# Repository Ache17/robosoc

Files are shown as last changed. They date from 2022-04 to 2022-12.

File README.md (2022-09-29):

# Quala

### Description
The goal of the project is to create an open drone that could be used potentially in future for running future project. Some initial idea was to create a drone swarm ( smaller drones "scouters" and larger drones "tankers", [Alex's pitch text needed for that]). Overall we want to have: 
- an OK performance mechanics ( we got the good donations and have stuff from DJI ), 
- own flight controller ( or at least ported by us to ardupilot in order to understand it better and modify our system in future)
- Video processing, communication and streaming done on raspberry pi ( open source, easy to modify, used in university courses)
- Control ( or sending command) done by Laptop

### System Diagram :
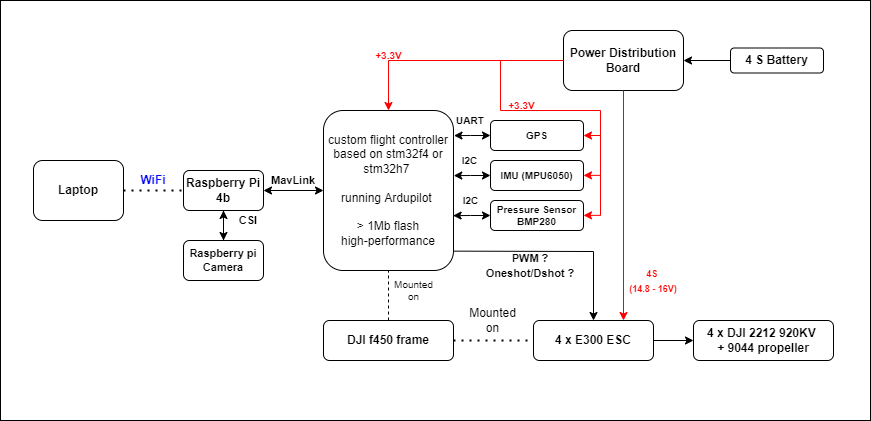
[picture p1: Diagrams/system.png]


## Components :
- Frame : [DJI F450](https://www.unmannedtechshop.co.uk/product/f450-quadcopter-frame-with-integrated-pdb/) 
- Autopilot : [Ardupilot](https://ardupilot.org/)
- ESCs : [E300](https://www.dji.com/uk/e300) (used now) or [XXD 30A](https://uk.banggood.com/Wholesale-XXD-HW30A-30A-Brushless-Motor-ESC-For-Airplane-Quadcopter-p-50621.html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) ( just because of cheap, maybe utilized in future)
- Motors : DJI 2212 motor 920kv ( standard DJI motors that came with the motors)
- Controller : Designed by us Board with stm32f411 or stm32h745/755 
- Video Processing / Communication (WiFi) : [Raspberry pi 4b](https://www.raspberrypi.com/products/raspberry-pi-4-model-b/) or [Pi Zero W 2](https://www.raspberrypi.com/products/raspberry-pi-zero-2-w/)
- Battery : [Tattu 4S 3700mAh](https://www.unmannedtechshop.co.uk/product/tattu-3700mah-45c-4s1p-lipo/)
- GPS : ( link needed ) 
- IMU : [MPU6050](https://invensense.tdk.com/products/motion-tracking/6-axis/mpu-6050/) ( support for drivers from Ardupilot), or [ISM330](https://estore.st.com/en/ism330dhcxtr-cpn.html) (high performance, not supprted by Ardupilot, plan to add it to our design )
- Pressure Sensor : [BMP280](https://www.bosch-sensortec.com/products/environmental-sensors/pressure-sensors/bmp280/) (stanadard pressure sensor)
- Power Distribution Board : Used by the one on DJI or this [one](https://www.unmannedtechshop.co.uk/product/power-distribution-board-with-led-voltage-regulator/)

### Autopilot + controller
Goal is to familliarize ourselves with [Ardupilot](https://ardupilot.org/) autopilot ( very good, active, great community and open project) so that we can contribute further to it. We wanted to designed custom controller for it. Due to lack of components we settled for black-pill board ( with stm32f411. There is a problem with flash size that is 512kB, ardupilot requires much more). 
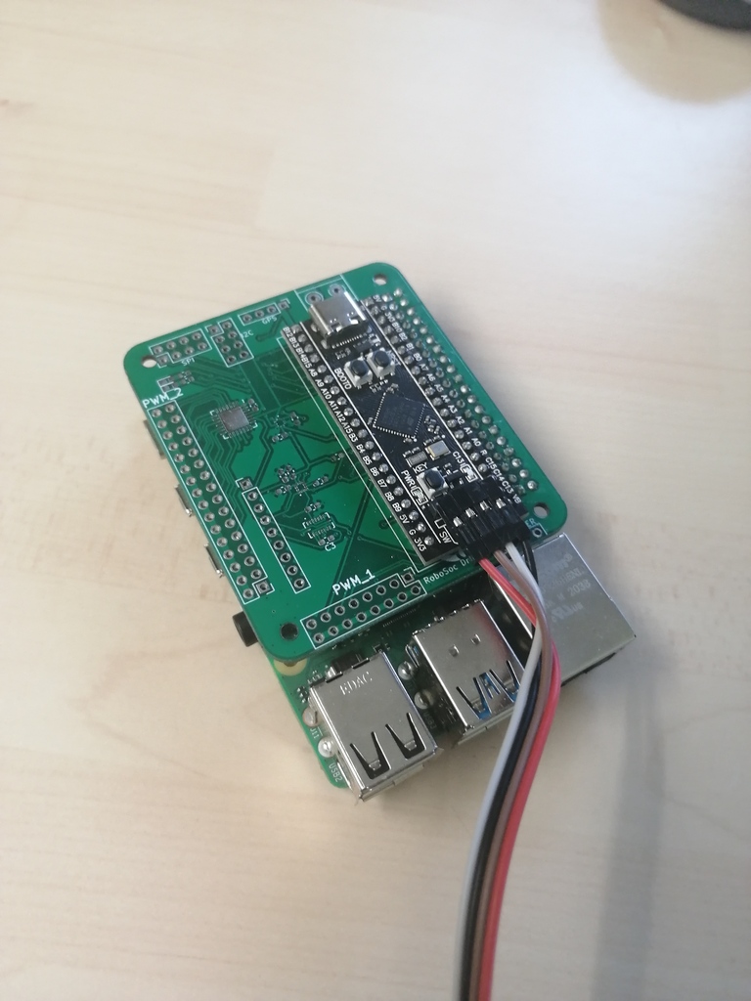
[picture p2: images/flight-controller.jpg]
controller board

We designed also controller on which we can place directly the microcontroller ( to avoid flash size issues, we can place stm32f405 or stm32h755)
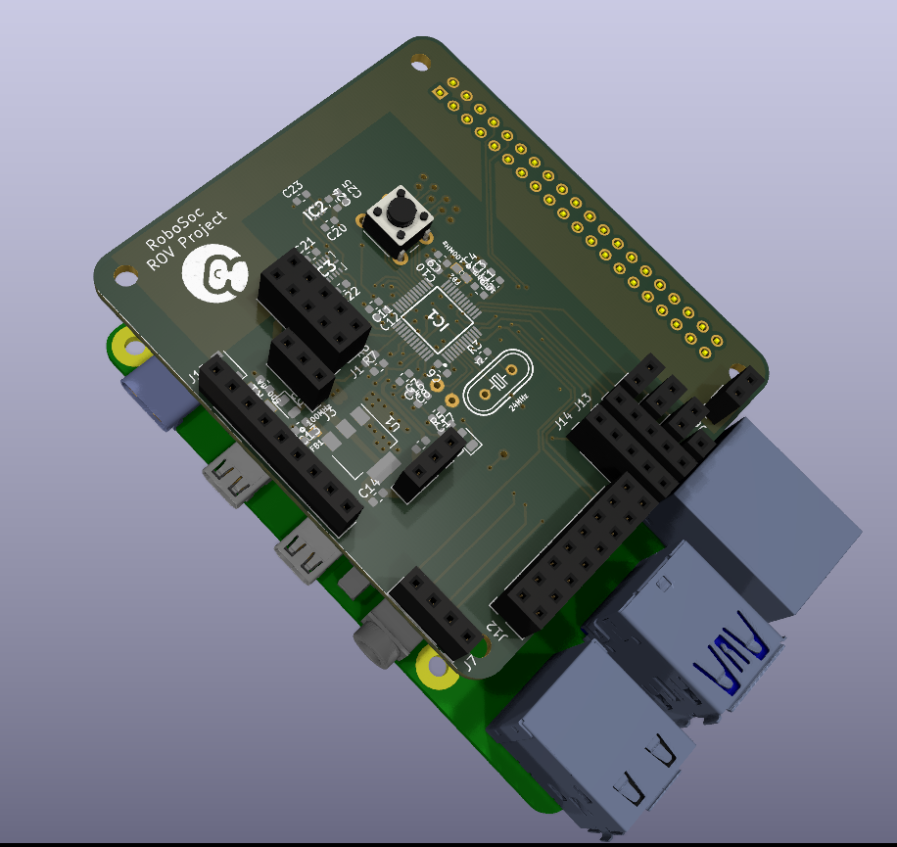
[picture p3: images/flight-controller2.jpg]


Communication between flight controller and raspberry pi is as described [here](https://ardupilot.org/dev/docs/raspberry-pi-via-mavlink.html).

### Video streaming
normally it requires video data streaming protocol (.h264 or .h265). Unfortunately we weren't able to achieve good results on it ( very high latency) so we settled for motion-jpeg streaming with low resolutions. 

### Theoretical evaluation 
Theoretical evaluation of the design was done on [flyeval.com](flyeval.com) ( [Introduction to Multicopter Design and Control, Quan Quan 2017](https://link.springer.com/book/10.1007/978-981-10-3382-7) ) and the screenshots below are taken from that website. 

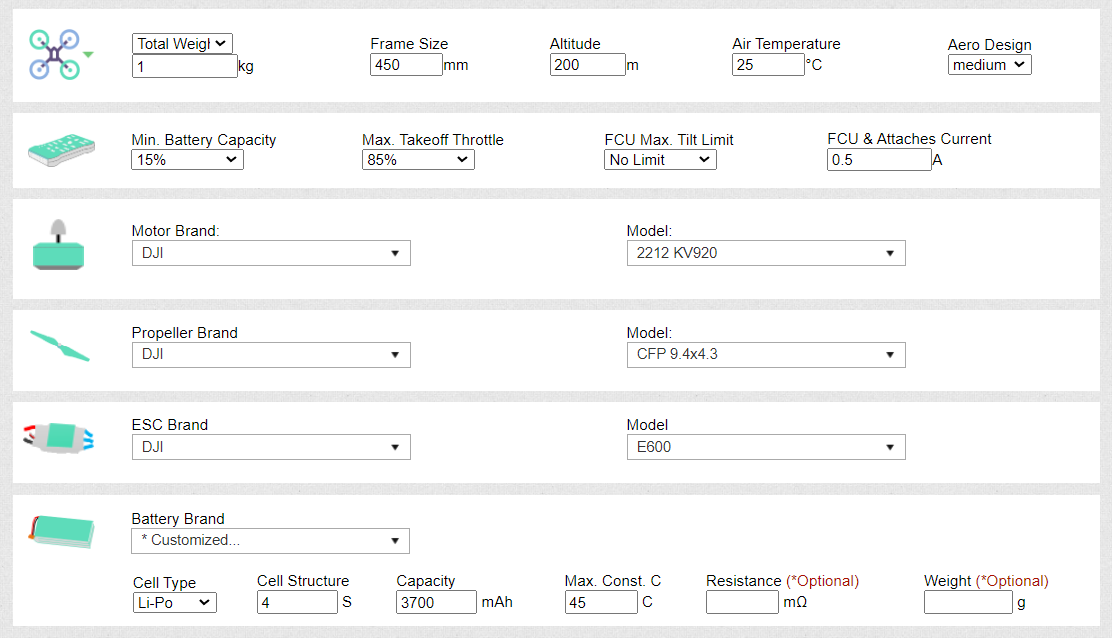
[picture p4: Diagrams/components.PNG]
Components


#### Performance of Model
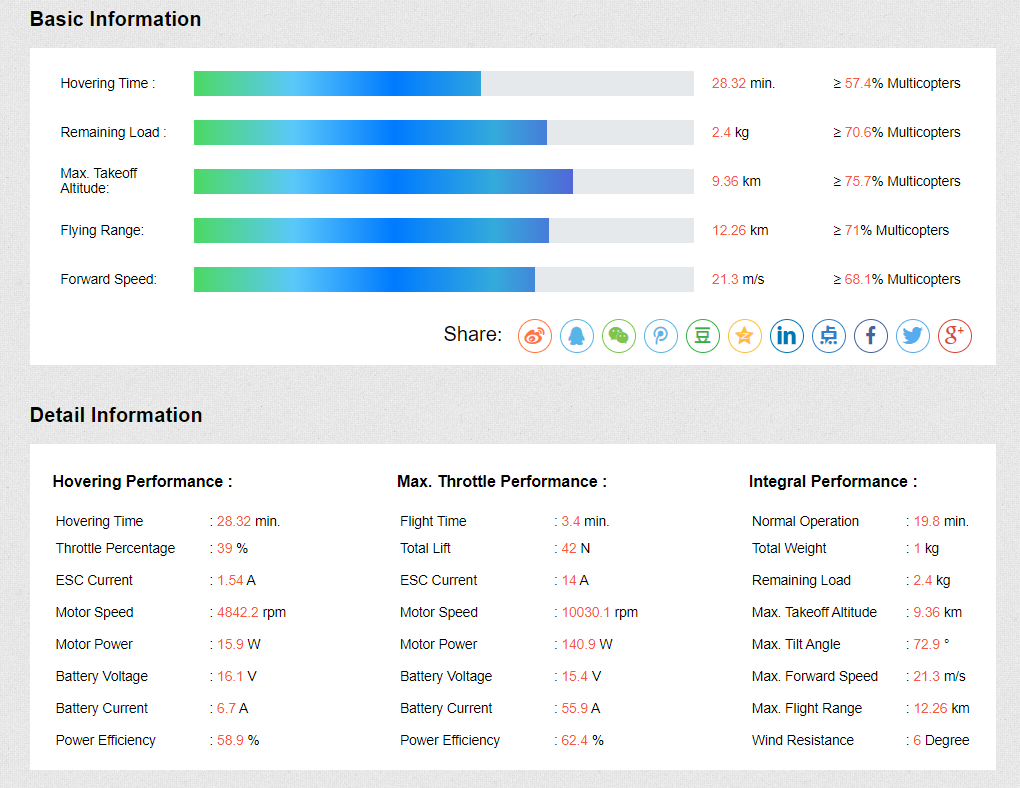
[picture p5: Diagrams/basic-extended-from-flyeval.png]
basic-extended-from-flyeval


#### Mathematical model of design
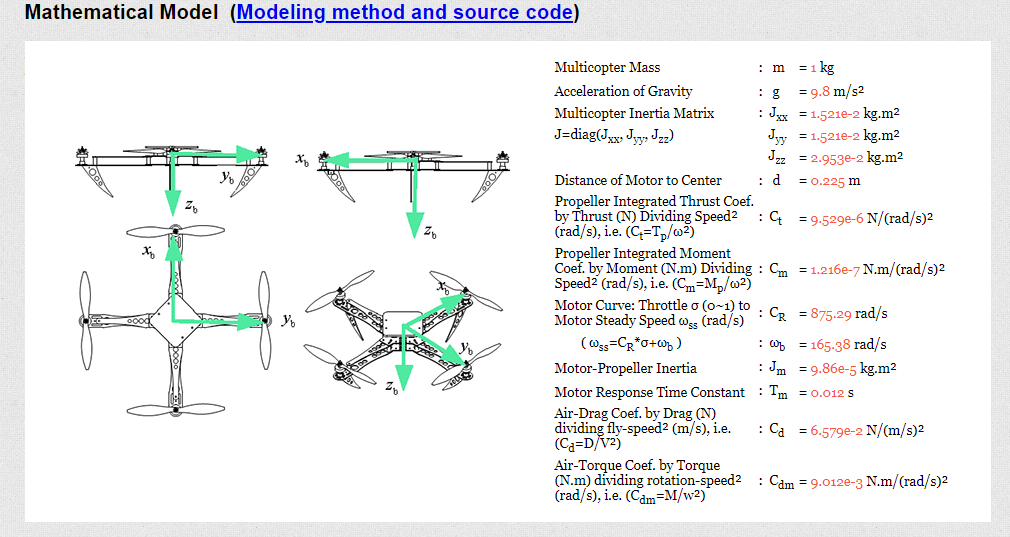
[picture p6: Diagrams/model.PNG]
Mathematical model of design


### pics from picture
(components, not yet working)
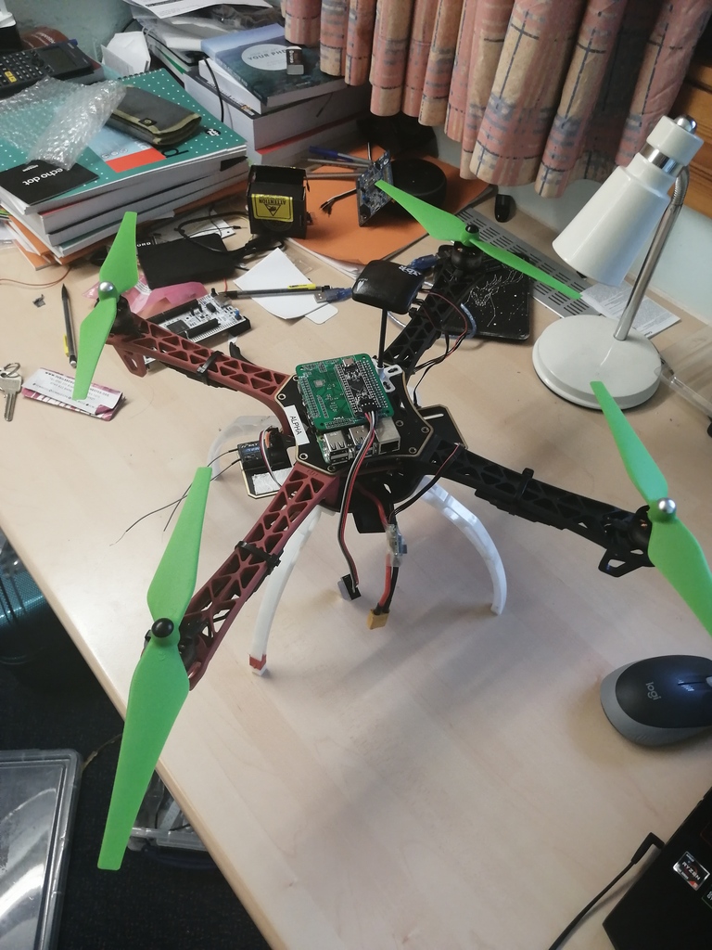
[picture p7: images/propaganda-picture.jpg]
propagangda picture


### Ardupilot notes: 
Sparky2, speedybeef4, SuccexF4, VRBrain-v51,
[17:33]
Compatible IMUs :
[17:35]
BMI055, BMI088, BMI160, BMI270, MPU6000, MPU9250,  ICM20608, ICM20602, ICM20601, ICM20789, ICM20689,  ICM20948, ICM20648 and ICM20649, ICM-40609, ICM-42688, ICM-42605, ICM-40605, IIM-42652, L3G4200D, LSM9DS0, LSM9DS1,
[17:39]
Compatible PRessure : BMP085, BMP280, BMP388, DPS280, FBM320, ICM20789, LPS2XH, MS5611,  SPL06
[17:42]
GPS : NMEA, NOVA, SBF, SBP, SBP2, SIRF, UAVCAN, UBLOX, RTCM3

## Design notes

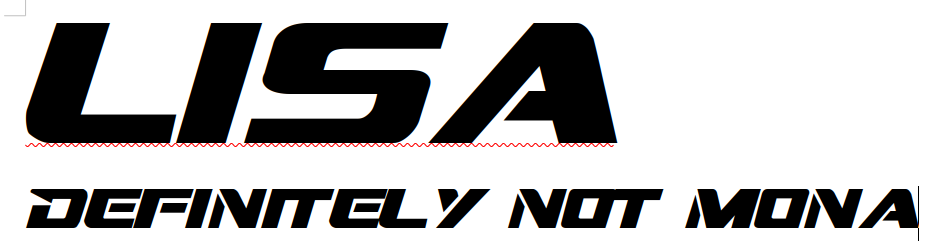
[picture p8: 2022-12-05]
hardware/LISA.png

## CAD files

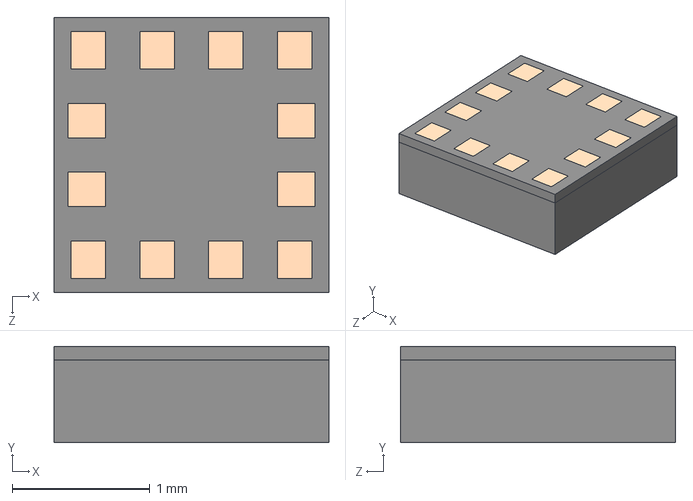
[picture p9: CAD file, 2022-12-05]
hardware/models/IIS2MDCTR.stp
2.00 x 0.7 x 2.00 mm

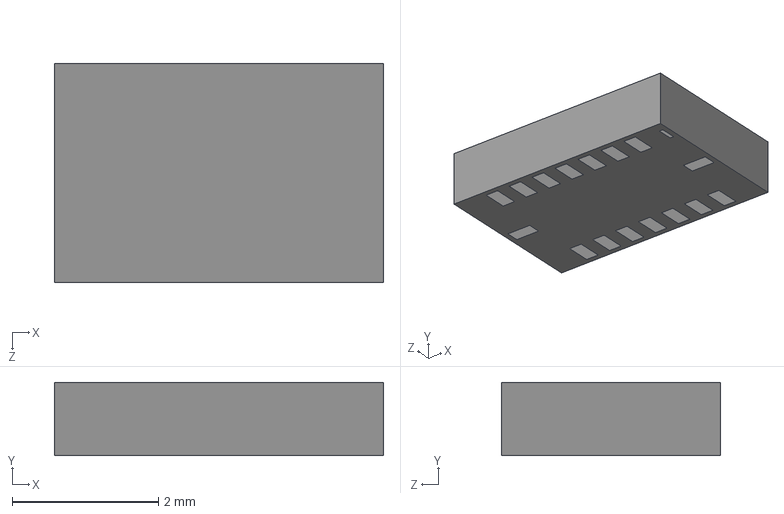
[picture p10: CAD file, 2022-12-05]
hardware/models/mod/BMI088.step
4.50 x 1.00 x 3.00 mm

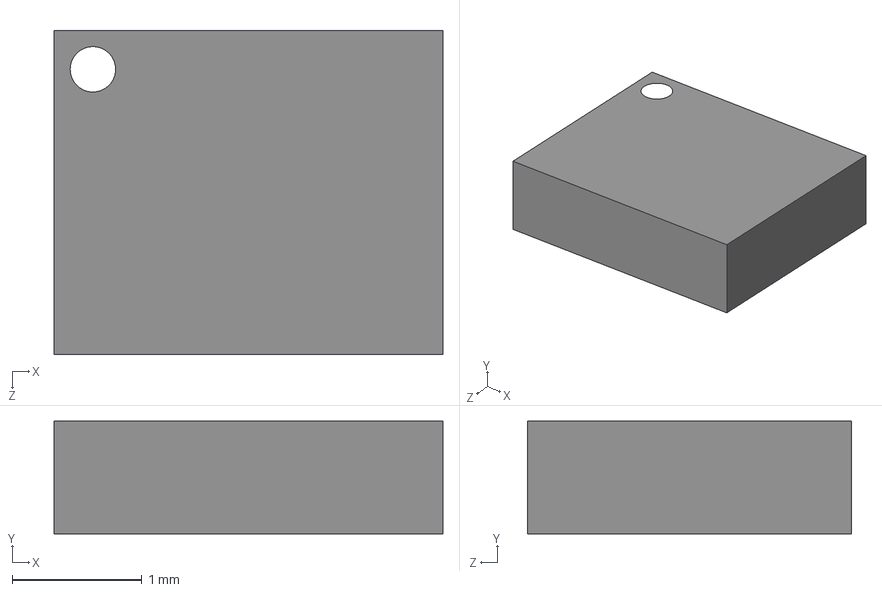
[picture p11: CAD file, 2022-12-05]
hardware/models/BMI270.STEP
3.00 x 0.87 x 2.50 mm

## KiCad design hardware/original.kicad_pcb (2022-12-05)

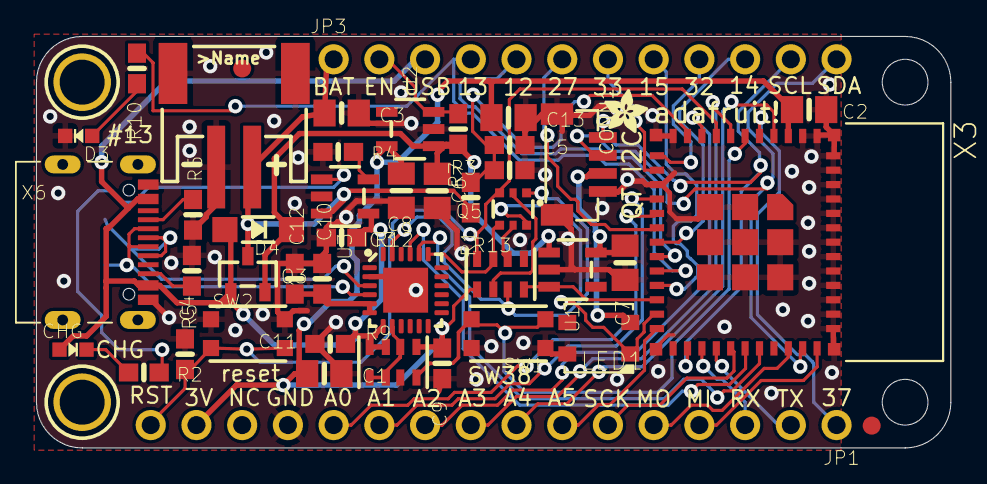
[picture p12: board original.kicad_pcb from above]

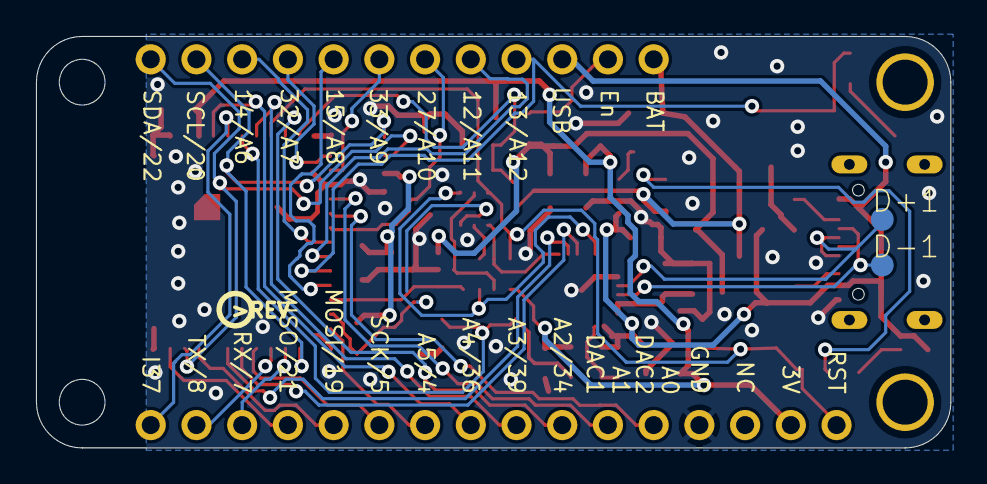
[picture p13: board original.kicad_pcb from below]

Board: 2 copper layers, 50.8 x 22.9 mm, 52 parts (3 on the bottom side), 49 nets.

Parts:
@HOLE0, @HOLE1: (no value)
C1, C2, C13: 10uF; 0805-NO
C3, C6, C7, C8: 10µF; 0805-NO
C4, C5, C9, C10: 1uF; 0603-NO
C11, C12: 0.1uF; 0603-NO
CHG: ORANGE; CHIPLED_0603_NOOUTLINE
CONN1: STEMMA_I2C_QTRA; JST_SH4_RA
D3: RED; CHIPLED_0603_NOOUTLINE
D4: MBR540; SOD-123
D+1: TPB1,27; B1,27
D-1: TPB1,27; B1,27
IC3: CP2102N-24; QFN24_4MM_SMSC
JP1: 1X16_ROUND
JP3: 1X12_ROUND
LED1: WS2812B3535; LED3535
Q3: DMG3415U; SOT23-R
Q5: DUAL NPN; SOT363
R1, R3: 200K; 0603-NO
R2, R4, R5, R6, R10: 5.1K; 0603-NO
R7, R12: 100K; 0603-NO
R9: 47K; RESPACK_4X0603
R13: 10K; RESPACK_4X0603
SW1, SW2: KMR2; BTN_KMR2_4.6X2.8
U1, U2: AP2112-3.3; SOT23-5
U3: MCP73831T-2ACI/OT; SOT23-5
U$13: PCBFEAT-REV-040
U$14: ADAFRUIT_2.5MM
U$31, U$32: MOUNTINGHOLE2.5; MOUNTINGHOLE_2.5_PLATED
U$34, U$35: FIDUCIAL_1MM
X1: JSTPH; JSTPH2_BATT
X3: ESP32-PICO-MINI-02MINI; ESP32-PICO-MINI
X6: USB Type C; USB_C_CUSB31-CFM2AX-01-X

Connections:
3.3V: C1.1, C2.1, C8.1, C9.1, C13.1, JP1.15, R9.5, R13.1, U2.5, X3.3
3.45V: C10.1, C12.1, IC3.5, IC3.6
A0_DAC2: JP1.12, X3.16
A1_DAC1: JP1.11, X3.15
A2_I34: JP1.10, X3.9
A3_I39: JP1.9, X3.7
A4_I36: JP1.8, X3.4
A5_IO4: JP1.7, X3.24
A13_I35: C5.1, R1.1, R3.2, X3.10
CC1: R6.2, X6.A5
CC2: R5.2, X6.B5
D+: D+1.TP, IC3.3, X6.A6, X6.B6
D-: D-1.TP, IC3.4, X6.A7, X6.B7
DTR: IC3.23, Q5.1, R13.3
EN: JP3.2, R7.1, U2.3
GND: C1.2, C2.2, C3.2, C4.2, C5.2, C6.2, C7.2, C8.2, C9.2, C10.2, C11.2, C12.2, C13.2, CONN1.1, CONN1.MT1, CONN1.MT2, D3.C, IC3.2, IC3.THERM, JP1.13, LED1.4, R3.1, R4.1, R5.1, R6.1, R9.3, R12.1, R13.5, SW1.A, SW1.A', SW2.A, SW2.A', U1.2, U2.2, U3.2, X1.1, X1.NC1, X1.NC2, X3.1, X3.2, X3.11, X3.14, X3.36, X3.37, X3.38, X3.39, X3.40, X3.41, X3.42, X3.43, X3.44, X3.45, X3.46, X3.47, X3.48, X3.49, X3.50, X3.51, X3.52, X3.53, X3.54, X3.55, X3.56, X3.57, X3.58, X3.59, X3.60, X3.61, X6.A1B12, X6.B1A12
GPIO0: LED1.1, Q5.6, X3.23
I37: JP1.1, X3.5
IO12_A11: JP3.5, X3.19
IO13_A12: JP3.4, R10.1, X3.20
IO14_A6: JP3.10, X3.18
IO15_A8: JP3.8, X3.21
IO27_A10: JP3.6, X3.17
IO32_A7: JP3.9, X3.12
IO33_A9: JP3.7, X3.13
MISO: JP1.4, X3.35
MOSI: JP1.5, X3.33
unnamed: CHG.C, R2.1
unnamed: R2.2, U3.1
unnamed: R4.2, U3.5
unnamed: D3.A, R10.2
unnamed: R9.4, SW1.B, SW1.B', X3.6
unnamed: Q5.5, R13.6
unnamed: Q5.2, R13.2
NEOI2C_PWR: R13.4, U1.3, X3.22
RTS: IC3.19, Q5.4, R13.7
RX/IO7: JP1.3, X3.27
RXD0: IC3.21, X3.30
SCK: JP1.6, X3.29
SCL: CONN1.4, JP3.11, X3.26
SDA: CONN1.3, JP3.12, X3.34
TX/IO8: JP1.2, X3.28
TXD0: IC3.20, X3.31
VBAT: C3.1, JP3.1, Q3.3, R1.2, U3.3, X1.2
VBUS: C11.1, CHG.A, D4.A, IC3.7, JP3.3, Q3.1, R9.7, R9.8, R12.2, U3.4, X6.A4B9, X6.B4A9
VBUS_DET: IC3.8, R9.1, R9.2, R9.6
VHI: C6.1, D4.C, Q3.2, R7.2, U1.1, U2.1
V_NEOI2C: C7.1, CONN1.2, LED1.2, U1.5
~RESET: C4.1, JP1.16, Q5.3, R13.8, SW2.B, SW2.B', X3.8

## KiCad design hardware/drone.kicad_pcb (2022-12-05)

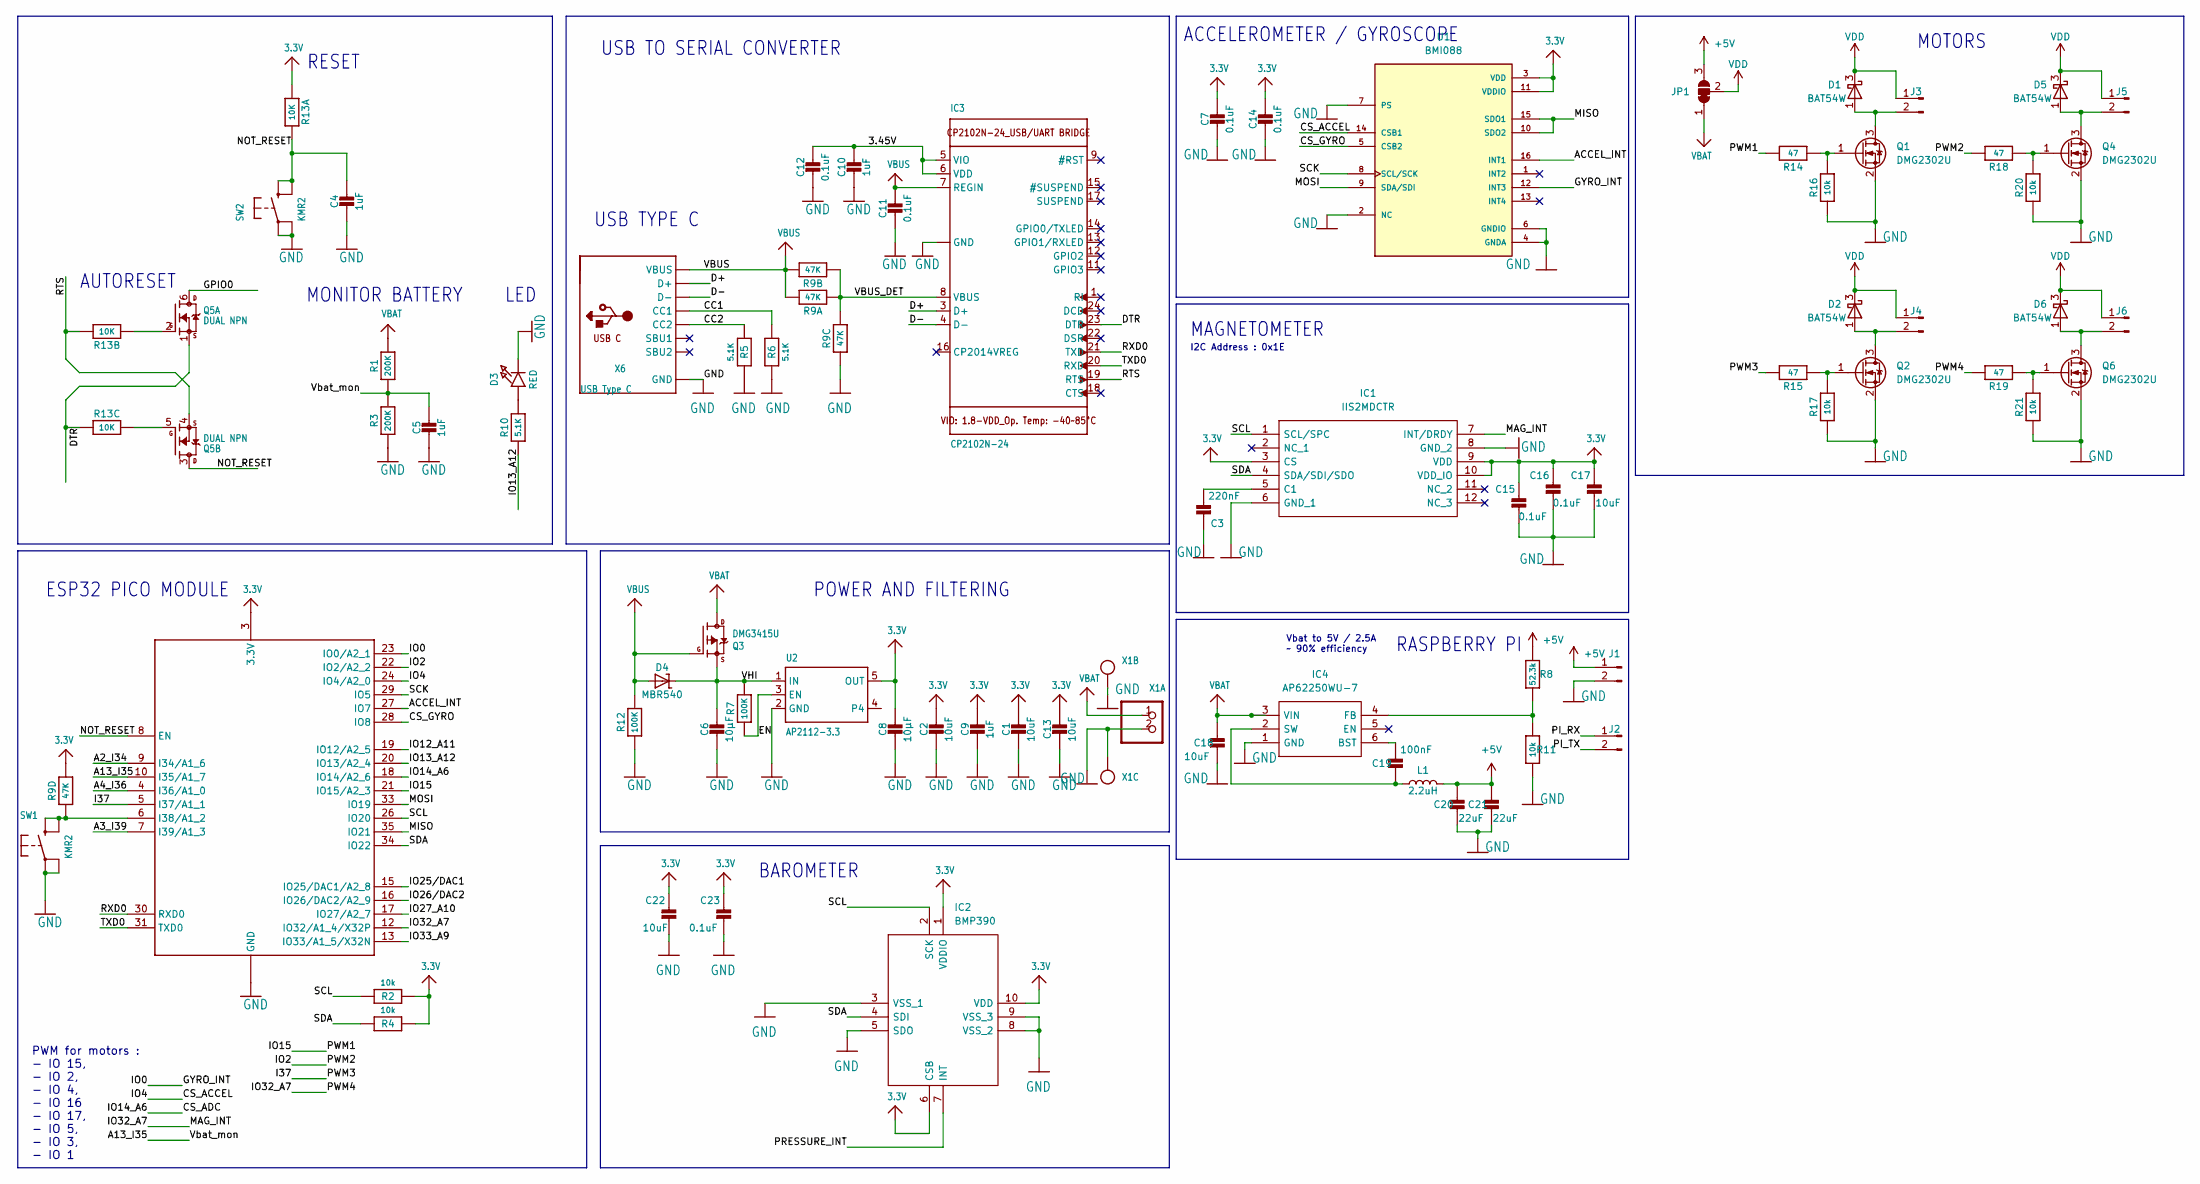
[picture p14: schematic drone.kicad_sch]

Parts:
C1, C2, C13: 10uF; 0805-NO
C3: 220nF; 0603-NO
C4, C5, C9, C10: 1uF; 0603-NO
C6: 10µF; 0805-NO
C7, C11, C12, C14, C15, C16, C23: 0.1uF; 0603-NO
C8: F; 0805-NO
C17, C18, C22: 10uF; 0603-NO
C19: 100nF; 0603-NO
C20, C21: 22uF; 0603-NO
D1, D2, D5, D6: BAT54W; SOT-323_SC-70
D3: RED; CHIPLED_0603_NOOUTLINE
D4: MBR540; SOD-123
IC1: IIS2MDCTR; Manufacturer_Part_Number IIS2MDCTR; Mouser Part Number 511-IIS2MDCTR
IC2: BMP390; Manufacturer_Part_Number BMP390; Mouser Part Number 262-BMP390
IC3: CP2102N-24; QFN24_4MM_SMSC
IC4: AP62250WU-7; SOT95P280X100-6N; Manufacturer_Part_Number AP62250WU-7; Mouser Part Number 621-AP62250WU-7
J1, J2, J3, J4, J5, J6: Conn_01x02_Male; conn_01x02
JP1: SolderJumper_3_Bridged12; SolderJumper-3_P1.3mm_Bridged12_RoundedPad1.0x1.5mm_NumberL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
L1: 2.2uH; L_1812_4532Metric
Q1, Q2, Q4, Q6: DMG2302U; SOT-23
Q3: DMG3415U; SOT23-R
Q5: DUAL NPN; SOT363
R1, R3: 200K; 0603-NO
R2, R4, R11, R16, R17, R20, R21: 10k; 0603-NO
R5, R6, R10: 5.1K; 0603-NO
R7, R12: 100K; 0603-NO
R8: 52.3k; 0603-NO
R9: 47K; RESPACK_4X0603
R13: 10K; RESPACK_4X0603
R14, R15, R18, R19: 47; 0603-NO
SW1, SW2: KMR2; BTN_KMR2_4.6X2.8
U1: BMI088; PQFN50P450X300X100-16N
U2: AP2112-3.3; SOT23-5
X1: CON_JST_PH_2PIN_MTPH2; JSTPH2_BATT
X3: ESP32-PICO-MINI-02MINI; ESP32-PICO-MINI
X6: USB Type C; USB_C_CUSB31-CFM2AX-01-X

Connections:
3.3V: C1.1, C2.1, C7.1, C8.1, C9.1, C13.1, C14.1, C15.1, C16.1, C17.1, C22.1, C23.1, IC1.3 (CS), IC1.9 (VDD), IC1.10 (VDD_IO), IC2.1 (VDDIO), IC2.6 (CSB), IC2.10 (VDD), R2.1, R4.1, R9.5 (2), R13.1, U1.3 (VDD), U1.11 (VDDIO), U2.5 (OUT), X3.3 (3.3V)
+5V: C20.1, C21.1, J1.1, JP1.3 (B), L1.2, R8.2
/3.45V: C10.1, C12.1, IC3.5 (VIO), IC3.6 (VDD)
/A2_I34: X3.9 (I34/A1_6)
/A3_I39: X3.7 (I39/A1_3)
/A4_I36: X3.4 (I36/A1_0)
/A13_I35: C5.1, R1.1, R3.2, X3.10 (I35/A1_7)
/ACCEL_INT: U1.16 (INT1), X3.27 (IO7)
/CC1: R6.2, X6.A5 (CC1)
/CC2: R5.2, X6.B5 (CC2)
/CS_ACCEL: U1.14 (CSB1), X3.24 (IO4/A2_0)
/CS_ADC: X3.18 (IO14/A2_6)
/CS_GYRO: U1.5 (CSB2), X3.28 (IO8)
/D+: IC3.3 (D+), X6.A6 (D+), X6.B6 (D+)
/D-: IC3.4 (D-), X6.A7 (D-), X6.B7 (D-)
/DTR: IC3.23 (DTR), Q5.1 (S), R13.3 (1)
/EN: R7.1, U2.3 (EN)
/GPIO0: Q5.6 (D)
/GYRO_INT: U1.12 (INT3), X3.23 (IO0/A2_1)
/IO12_A11: X3.19 (IO12/A2_5)
/IO13_A12: R10.1, X3.20 (IO13/A2_4)
/IO25/DAC1: X3.15 (IO25/DAC1/A2_8)
/IO26/DAC2: X3.16 (IO26/DAC2/A2_9)
/IO27_A10: X3.17 (IO27/A2_7)
/IO33_A9: X3.13 (IO33/A1_5/X32N)
/MISO: U1.10 (SDO2), U1.15 (SDO1), X3.35 (IO21)
/MOSI: U1.9 (SDA/SDI), X3.33 (IO19)
/NOT_RESET: C4.1, Q5.3 (D), R13.8 (2), SW2.B (S), SW2.B' (S1), X3.8 (EN)
/PI_RX: J2.1
/PI_TX: J2.2
/PRESSURE_INT: IC2.7 (INT)
/PWM1: R14.2, X3.21 (IO15/A2_3)
/PWM2: R18.2, X3.22 (IO2/A2_2)
/PWM3: R15.2, X3.5 (I37/A1_1)
/PWM4: IC1.7 (INT/DRDY), R19.2, X3.12 (IO32/A1_4/X32P)
/RTS: IC3.19 (RTS), Q5.4 (S), R13.7 (2)
/RXD0: IC3.21 (TXD), X3.30 (RXD0)
/SCK: U1.8 (SCL/SCK), X3.29 (IO5)
/SCL: IC1.1 (SCL/SPC), IC2.2 (SCK), R2.2, X3.26 (IO20)
/SDA: IC1.4 (SDA/SDI/SDO), IC2.4 (SDI), R4.2, X3.34 (IO22)
/TXD0: IC3.20 (RXD), X3.31 (TXD0)
/VBUS_DET: IC3.8 (VBUS), R9.1, R9.2 (1), R9.6 (2)
/VHI: C6.1, D4.C, Q3.2 (S), R7.2, U2.1 (IN)
GND: C1.2, C2.2, C3.1, C4.2, C5.2, C6.2, C7.2, C8.2, C9.2, C10.2, C11.2, C12.2, C13.2, C14.2, C15.2, C16.2, C17.2, C18.2, C20.2, C21.2, C22.2, C23.2, D3.C, IC1.6 (GND_1), IC1.8 (GND_2), IC2.3 (VSS_1), IC2.5 (SDO), IC2.8 (VSS_2), IC2.9 (VSS_3), IC3.2 (GND), IC3.THERM (GND), IC4.1 (GND), J1.2, Q1.2 (S), Q2.2 (S), Q4.2 (S), Q6.2 (S), R3.1, R5.1, R6.1, R9.3 (1), R11.1, R12.1, R16.1, R17.1, R20.1, R21.1, SW1.A, SW1.A' (P1), SW2.A, SW2.A' (P1), U1.2 (NC), U1.4 (GNDA), U1.6 (GNDIO), U1.7 (PS), U2.2 (GND), X1.2, X1.NC1, X1.NC2, X3.1 (GND), X3.2 (GND), X3.11 (GND), X3.14 (GND), X3.36 (GND), X3.37 (GND), X3.38 (GND), X3.39 (GND), X3.40 (GND), X3.41 (GND), X3.42 (GND), X3.43 (GND), X3.44 (GND), X3.45 (GND), X3.46 (GND), X3.47 (GND), X3.48 (GND), X3.49 (GND), X3.50 (GND), X3.51 (GND), X3.52 (GND), X3.53 (GND), X3.54 (GND), X3.55 (GND), X3.56 (GND), X3.57 (GND), X3.58 (GND), X3.59 (GND), X3.60 (GND), X3.61 (GND), X6.A1B12 (GND), X6.B1A12 (GND)
unnamed: C3.2, IC1.5 (C1)
unnamed: C19.1, IC4.6 (BST)
unnamed: C19.2, IC4.2 (SW), L1.1
unnamed: D1.1 (A), J3.2, Q1.3 (D)
unnamed: D2.1 (A), J4.2, Q2.3 (D)
unnamed: D3.A, R10.2
unnamed: D5.1 (A), J5.2, Q4.3 (D)
unnamed: D6.1 (A), J6.2, Q6.3 (D)
unnamed: IC4.4 (FB), R8.1, R11.2
unnamed: Q1.1 (G), R14.1, R16.2
unnamed: Q2.1 (G), R15.1, R17.2
unnamed: Q4.1 (G), R18.1, R20.2
unnamed: Q5.2 (G), R13.2 (1)
unnamed: Q5.5 (G), R13.6 (2)
unnamed: Q6.1 (G), R19.1, R21.2
unnamed: R9.4 (1), SW1.B (S), SW1.B' (S1), X3.6 (I38/A1_2)
VBAT: C18.1, IC4.3 (VIN), JP1.1 (A), Q3.3 (D), R1.2, X1.1
VBUS: C11.1, D4.A, IC3.7 (REGIN), Q3.1 (G), R9.7 (2), R9.8 (2), R12.2, X6.A4B9 (VBUS), X6.B4A9 (VBUS)
VDD: D1.3 (K), D2.3 (K), D5.3 (K), D6.3 (K), J3.1, J4.1, J5.1, J6.1, JP1.2 (C)

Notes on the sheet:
ACCELEROMETER / GYROSCOPE
USB TO SERIAL CONVERTER
MOTORS
AUTORESET
USB TYPE C
RASPBERRY PI
PWM for motors : - IO 15, - IO 2, - IO 4, - IO 16 - IO 17, - IO 5, - IO 3, - IO 1
MAGNETOMETER
BAROMETER
MONITOR BATTERY
POWER AND FILTERING
I2C Address : 0x1E
RESET
ESP32 PICO MODULE
LED
Vbat to 5V / 2.5A ~ 90% efficiency

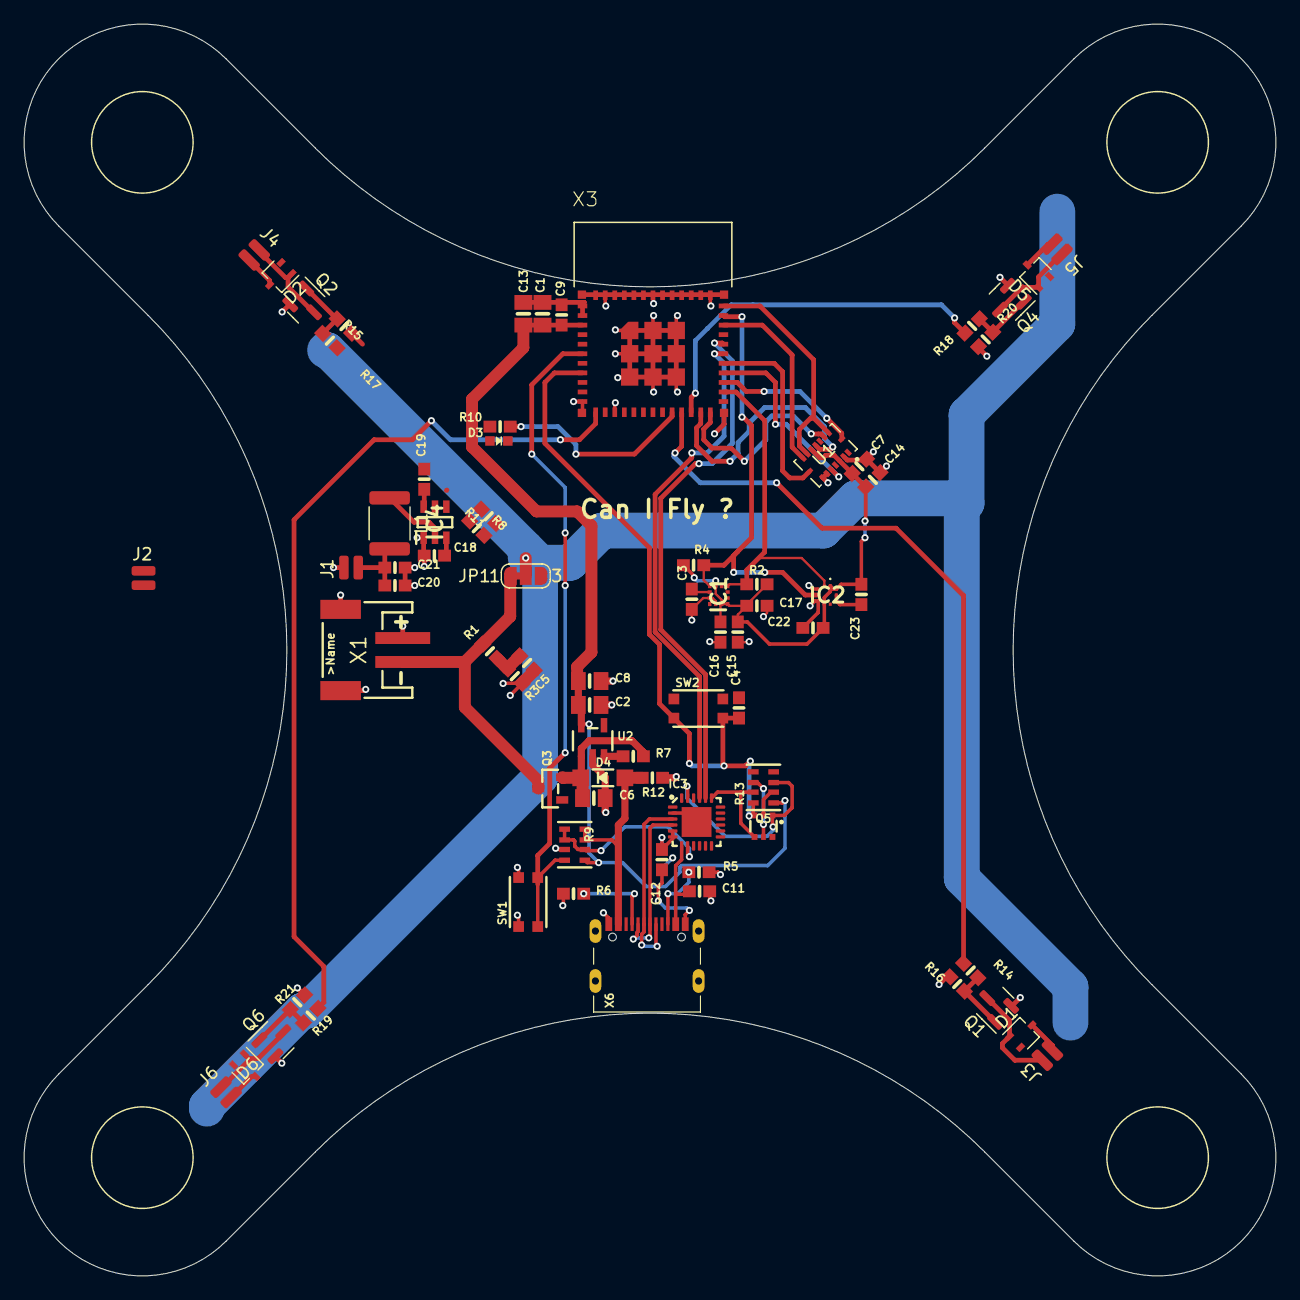
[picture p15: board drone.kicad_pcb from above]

Board: 2 copper layers, 104.8 x 104.8 mm, 75 parts (1 on the bottom side), 50 nets.

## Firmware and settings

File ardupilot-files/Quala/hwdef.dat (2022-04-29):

# hw definition file for processing by chibios_pins.py
# for Matek H743-WING

# MCU class and specific type
MCU STM32H7xx STM32H743xx

# board ID for firmware load
APJ_BOARD_ID 1013

# crystal frequency, setup to use external oscillator
OSCILLATOR_HZ 25000000

FLASH_SIZE_KB 2048
env OPTIMIZE -Os

# bootloader takes first sector
FLASH_RESERVE_START_KB 128


# ChibiOS system timer
# STM32_ST_USE_TIMER 12
# define CH_CFG_ST_RESOLUTION 16

# USB
# PA11 OTG_FS_DM OTG1
# PA12 OTG_FS_DP OTG1

# PA13 JTMS-SWDIO SWD
# PA14 JTCK-SWCLK SWD

# SPI1 for IMU1 (MPU6000)
# PA5 SPI1_SCK SPI1
# PA6 SPI1_MISO SPI1
# PD7 SPI1_MOSI SPI1
# PC15 IMU1_CS CS

# SPI2 for MAX7456 OSD
# PB12 MAX7456_CS CS
# PB13 SPI2_SCK SPI2
# PB14 SPI2_MISO SPI2
# PB15 SPI2_MOSI SPI2

# SPI3 - external
# PB3 SPI3_SCK SPI3
# PB4 SPI3_MISO SPI3
# PB5 SPI3_MOSI SPI3

# external CS pins
# PD4 EXT_CS1 CS
# PE2 EXT_CS2 CS

# SPI4 for IMU2 (ICM20602)
# PE11 IMU2_CS CS
# PE12 SPI4_SCK SPI4
# PE13 SPI4_MISO SPI4
# PE14 SPI4_MOSI SPI4

# add ICM42605 on SPI4 as a backup to replace ICM20602
# PC13 IMU3_CS CS

# two I2C bus
# I2C_ORDER I2C2 I2C1

# I2C1
# PB6 I2C1_SCL I2C1
# PB7 I2C1_SDA I2C1

# I2C2
# PB10 I2C2_SCL I2C2
# PB11 I2C2_SDA I2C2

# ADC
# PC0 BATT_VOLTAGE_SENS ADC1 SCALE(1)
# PC1 BATT_CURRENT_SENS ADC1 SCALE(1)
# PA4 BATT2_VOLTAGE_SENS ADC1 SCALE(1)
# PA7 BATT2_CURRENT_SENS ADC1 SCALE(1)

# define HAL_BATT_MONITOR_DEFAULT 4
# define HAL_BATT_VOLT_PIN 10
# define HAL_BATT_CURR_PIN 11
# define HAL_BATT2_VOLT_PIN 18
# define HAL_BATT2_CURR_PIN 7
# define HAL_BATT_VOLT_SCALE 11.0
# define HAL_BATT_CURR_SCALE 40.0
# define HAL_BATT2_VOLT_SCALE 11.0

# PC4 PRESSURE_SENS ADC1 SCALE(2)
# define HAL_DEFAULT_AIRSPEED_PIN 4

# PC5 RSSI_ADC ADC1
# define BOARD_RSSI_ANA_PIN 8

# LED
# green LED1 marked as B/E
# blue LED0 marked as ACT
# PE3 LED0 OUTPUT LOW GPIO(90) # blue
# PE4 LED1 OUTPUT LOW GPIO(91) # green
# define HAL_GPIO_A_LED_PIN 91
# define HAL_GPIO_B_LED_PIN 90
# define HAL_GPIO_LED_OFF 1

# order of UARTs (and USB)
# SERIAL_ORDER OTG1 UART7 USART1 USART2 USART3 UART8 UART4 USART6 OTG2

# USART1 (telem2)
# PA10 USART1_RX USART1
# PA9  USART1_TX USART1

# USART2 (GPS1)
# PD5 USART2_TX USART2
# PD6 USART2_RX USART2

# USART3 (GPS2)
# PD9 USART3_RX USART3
# PD8 USART3_TX USART3

# UART4 (spare)
# PB9 UART4_TX UART4
# PB8 UART4_RX UART4

# USART6 (RC input), SERIAL7
# PC7 TIM3_CH2 TIM3 RCININT PULLDOWN LOW
# PC6 USART6_TX USART6 NODMA

# as an alternative config setup the RX6 pin as a uart. This allows
# for bi-directional UART based receiver protocols such as FPort
# without any extra hardware
# PC7 USART6_RX USART6 NODMA ALT(1)

# UART7 (telem1)
# PE7 UART7_RX UART7
# PE8 UART7_TX UART7
# PE10 UART7_CTS UART7
# PE9  UART7_RTS UART7

# UART8 (spare)
# PE0 UART8_RX UART8
# PE1 UART8_TX UART8

# CAN bus
# PD0 CAN1_RX CAN1
# PD1 CAN1_TX CAN1
# PD3 GPIO_CAN1_SILENT OUTPUT PUSHPULL SPEED_LOW LOW GPIO(70)

# Motors
# PB0  TIM8_CH2N TIM8  PWM(1)  GPIO(50)
# PB1  TIM8_CH3N TIM8  PWM(2)  GPIO(51)
# PA0  TIM5_CH1  TIM5  PWM(3)  GPIO(52)
# PA1  TIM5_CH2  TIM5  PWM(4)  GPIO(53)
# PA2  TIM5_CH3  TIM5  PWM(5)  GPIO(54)
# PA3  TIM5_CH4  TIM5  PWM(6)  GPIO(55)
# PD12 TIM4_CH1 TIM4 PWM(7) GPIO(56)
# PD13 TIM4_CH2 TIM4 PWM(8) GPIO(57)
# PD14 TIM4_CH3 TIM4 PWM(9) GPIO(58)
# PD15 TIM4_CH4 TIM4 PWM(10) GPIO(59)
# PE5  TIM15_CH1 TIM15 PWM(11) GPIO(60)
# PE6  TIM15_CH2 TIM15 PWM(12) GPIO(61)
# PA8 TIM1_CH1 TIM1 PWM(13) GPIO(62) # for WS2812 LED

# Beeper
# PA15 TIM2_CH1 TIM2 GPIO(32) ALARM

# microSD support
# PC8 SDMMC1_D0 SDMMC1
# PC9 SDMMC1_D1 SDMMC1
# PC10 SDMMC1_D2 SDMMC1
# PC11 SDMMC1_D3 SDMMC1
# PC12 SDMMC1_CK SDMMC1
# PD2 SDMMC1_CMD SDMMC1

# GPIOs
# PD10  PINIO1 OUTPUT GPIO(81) LOW
# PD11  PINIO2 OUTPUT GPIO(82) LOW

# DMA_PRIORITY S*

# define HAL_STORAGE_SIZE 16384

# use last 2 pages for flash storage
# H743 has 16 pages of 128k each
# STORAGE_FLASH_PAGE 14

# spi devices
# SPIDEV icm42688  SPI1 DEVID1 IMU1_CS      MODE3  2*MHZ  8*MHZ
# SPIDEV mpu6000   SPI1 DEVID1 IMU1_CS      MODE3  1*MHZ  4*MHZ
# SPIDEV icm20602  SPI4 DEVID1 IMU2_CS      MODE3  1*MHZ  4*MHZ
# SPIDEV icm42605  SPI4 DEVID1 IMU3_CS      MODE3  2*MHZ  8*MHZ
# SPIDEV osd       SPI2 DEVID4 MAX7456_CS   MODE0 10*MHZ 10*MHZ


# DMA_NOSHARE SPI1* SPI4*

# SPI3 external connections
# SPIDEV pixartflow   SPI3 DEVID1  EXT_CS1  MODE3   2*MHZ  2*MHZ

# no built-in compass, but probe the i2c bus for all possible
# external compass types
# define ALLOW_ARM_NO_COMPASS
# define HAL_PROBE_EXTERNAL_I2C_COMPASSES
# define HAL_I2C_INTERNAL_MASK 0
# define HAL_COMPASS_AUTO_ROT_DEFAULT 2

# two IMUs
# H743-V1,      ICM20602, MPU6000
# H743-V1.5/V2, ICM42605, MPU6000
# H743-V3,      ICM42688P, ICM42605
# IMU Invensensev3 SPI:icm42688 ROTATION_YAW_180
# IMU Invensensev3 SPI:icm42605 ROTATION_YAW_270
# IMU Invensense SPI:icm20602 ROTATION_ROLL_180_YAW_270
# IMU Invensense SPI:mpu6000 ROTATION_ROLL_180_YAW_270
# define HAL_DEFAULT_INS_FAST_SAMPLE 1
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
